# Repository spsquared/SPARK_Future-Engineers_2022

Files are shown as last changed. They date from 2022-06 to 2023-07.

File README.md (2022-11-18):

<div align=center>

banner

</div>

***

**Official GitHub repository for WRO USA team SPARK Future Engineers 2022. All code, documentation, and files are located here.**

Located below is the documentation, and a link to the build instructions.

***

# Contents
* [Hardware Overview](#the-hardware)
    * [Parts List](#parts-list)
    * [Assembly Instructions & Diagrams](#assembly)
    * [Photos](#photos)
* [Software Overview](#the-software)
    * [Operating System](#operating-system)
    * [Programming Language](#programming-language)
    * [IO](#io)
    * [Image Processing and Predictions](#image-predictions)
        * [Image Preprocessing](#image-preprocessing)
        * [Wall Steering](#wall-steering)
        * [Pillar Steering](#pillar-steering)
        * [Final Steering](#final-steering)
    * [SPARK Control Panel](#spark-control)
* [Team Photos](#team-photos)
* [Demonstration Video](#demonstration-video)
* [LiPo Battery Safety Notice](#lipo-battery-safety-notice)

***

# **The Hardware**

## Parts List
* [Schumacher Atom 2 S2 1/12 GT12 Competition Pan Car Kit](https://www.amainhobbies.com/schumacher-atom-2-s2-1-12-gt12-competition-pan-car-kit-schk179/p1055346)
* [HobbyWing QUICRUN 10BL60 Brushless ESC Sensored](https://www.hobbywingdirect.com/products/quicrun-10-sensored)
* [Fantom ICON V2 Torque Edition - Sensored Brushless Motor 25.5T](https://fantomracing.com/shop/motors/spec-motors/25-5-icon-torque-works-edition/)
* [12 Tooth 48 Pitch Pinion Gear w/Set Screw (3.17mm Bore)](https://www.amazon.com/Traxxas-PINION-PITCH-SCREW-2428/dp/B00EFXMUO2)
* [78 Tooth Spur Gear 48 Pitch](https://www.amazon.com/Kimbrough-Pitch-Spur-Gear-78T/dp/B0006O1QVM)
* [Xceed RC "Enneti" 1/12 Carbon Front Tires (2) (Carbon Black) (40 Shore)](https://www.amainhobbies.com/xceed-rc-enneti-1-12-carbon-front-tires-2-carbon-black-40-shore-xcd101708/p385419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)
* [Xceed RC "Enneti" 1/12 Carbon Rear Tires (2) (Carbon Black) (30 Shore)](https://www.amainhobbies.com/xceed-rc-enneti-1-12-carbon-rear-tires-2-carbon-black-30-shore-xcd101710/p385420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) OR [LEGO 49.5x20mm Tire (Part 15413)](https://www.bricklink.com/v2/catalog/catalogitem.page?P=15413) paired with 3d printed rims
* [Savox SV1260MG - Mini Digital High Voltage Servo 7.4V](https://www.savoxusa.com/products/savsv1260mg-mini-digital-high-voltage)
* [Woltechz LiPo Battery Balance Charger Discharger 1S -6S AC/DC for NiMH/NiCD/Li-PO/Li-Fe/Li-ion/PB](https://www.amazon.com/Woltechz-Battery-Charger-Discharger-Multi-Charging/dp/B07KDSGJFD/)
* [2x Zeee Premium Series 3S LiPo Battery 4200mAh 11.4V High Voltage Battery 120C with XT60 Plug](https://www.ebay.com/itm/384548969557)
* [2x Variable DC Voltage Buck Converter](https://www.amazon.com/Regulator-Adjustable-Converter-Electronic-Stabilizer/dp/B07PDGG84B/ref=sr_1_18)
* [Male 5.5mm DC Barrel Connector Pigtails](https://www.amazon.com/Pigtails-Female-Connector-Pigtail-Security/dp/B08PYWN3T7/)
* [DC Digital Voltometer](https://www.amazon.com/bayite-Digital-Voltmeter-Display-Motorcycle/dp/B00YALUXH0/)
* [Normally Closed Push Button Momentary On Switch (size must match)](https://www.amazon.com/Pieces-normally-closed-Button-Momentary/dp/B07HCLVMGS/)
* [Yahboom Jetson Nano 4GB Developer Kit](https://category.yahboom.net/collections/jetson/products/jetson-nano-sub)
* [Arducam Raspberry Pi Official Camera Module V2, with 8 Megapixel IMX219 Wide Angle 175 Degree Replacement](https://www.amazon.com/Arducam-Raspberry-Official-Megapixel-Replacement/dp/B083PW4BLH/)
* [Intel AX201 WiFi 6 BT 5.1 M.2 2230 with 10in RP-SMA Antenna (not required)](https://www.newegg.com/p/0XM-009Y-001C7)
* [Noctua NF-A4x10 5V (not required)](https://noctua.at/en/products/fan/nf-a4x10-5v)
* 20-24 gauge wire
* 25mm M3 brass spacers
* 20mm, 15mm M3 brass standoffs
* 6mm M3 nylon standoffs
* M3 nylon nuts
* 6mm countersunk M3 screws
* 6mm M3 nylon screws
* 4mm M2.5 screws

*Our build uses a different 25.5T brushless motor from HobbyWing but we had to modify our chassis to make it fit. The code will still work with the motor in this list.*

3D printed parts were used in our build, and all CAD files are located in the folder [/Documentation/CAD/](https://github.com/definitely-nobody-is-here/SPARK_Future-Engineers_2022/tree/master/Documentation/CAD). They're also linked here:
* [Platform](https://github.com/definitely-nobody-is-here/SPARK_Future-Engineers_2022/raw/master/Documentation/CAD/SPARK2022_platform.stl)
* [Camera Mount](https://github.com/definitely-nobody-is-here/SPARK_Future-Engineers_2022/raw/master/Documentation/CAD/SPARK2022_cameramount.stl)
* [Rear Wheel Rim](https://github.com/definitely-nobody-is-here/SPARK_Future-Engineers_2022/raw/master/Documentation/CAD/SPARK2022_rearwheelrim.stl) (if not using Xceed rear tires)
<!-- * [Camera LED Clip](https://github.com/definitely-nobody-is-here/SPARK_Future-Engineers_2022/raw/master/Documentation/CAD/SPARK2022_cameraLEDmount.stl) -->

The total estimated cost for the build is an eye watering $1050.00 excluding tools, 3D printers, computers, screws, wires, and standoffs.

## Assembly

We followed the instructions for the Atom 2 pan car kit, and then added the platform, wheels, and electronics. The ESC is VHB taped to the metal chassis, and the motor is mounted with the 12 tooth pinion gear. We swapped the stock 64 tooth spur gear to a new 78 tooth spur gear to lower our speed and give slightly more torque. The wires going to the voltage regulators can be soldered directly into the XT-60 connector with the ESC power leads. The voltage regulators and voltage meter can be screwed into standoffs with nylon screws on the upper platform.

The two RP-SMA connectors for the WiFi card (not required but good for development) can be routed to the back of the platform into their brackets. The NF A4x10 can be screwed into the heatsink of the Jetson NANO Developer Kit using 4 long nylon screws, but the holes will first have to be tapped or "tapped" by metal screws. The fan is also not required but can help (the board does reach fairly high temperatures at times).

The top platform is mounted onto existing locations on the car. In the rear two spacers are screwed into the mounting locations for the rear body posts. In the front, the screws for the bracket above the steering servo are replaced with standoffs.

The camera and LEDs are mounted on top of standoffs extending the top of front wheel plate.

#### **For a detailed build guide, go to [ASSEMBLY.md](./ASSEMBLY.md)**

Here is a simple electromechanical schematic for how the electronics are wired:

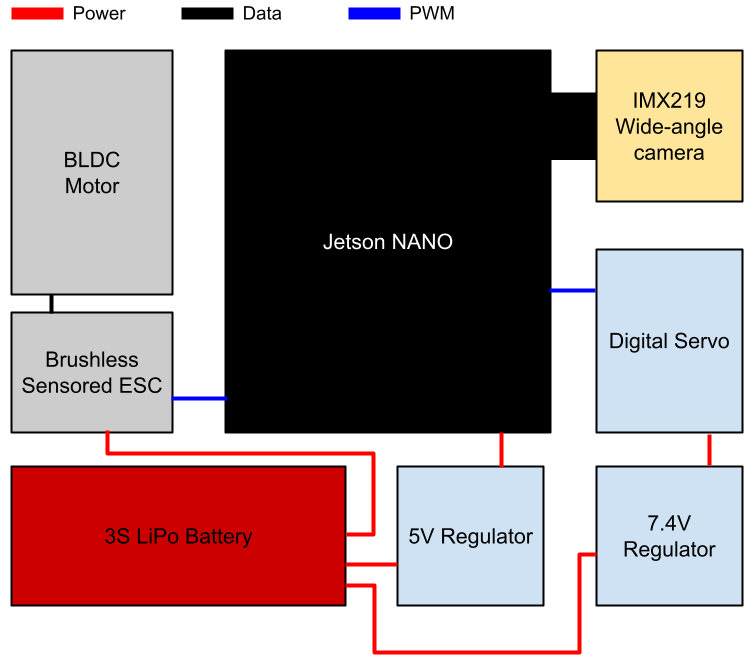
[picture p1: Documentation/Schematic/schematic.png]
Schematic


***

## Photos
| | |
| --- | --- |
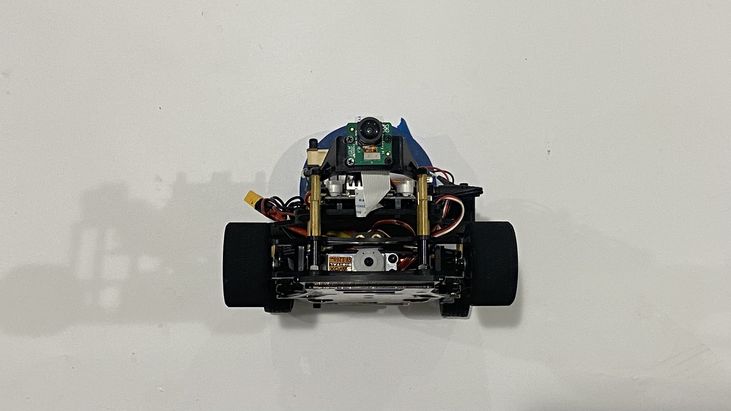
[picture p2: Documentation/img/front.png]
front
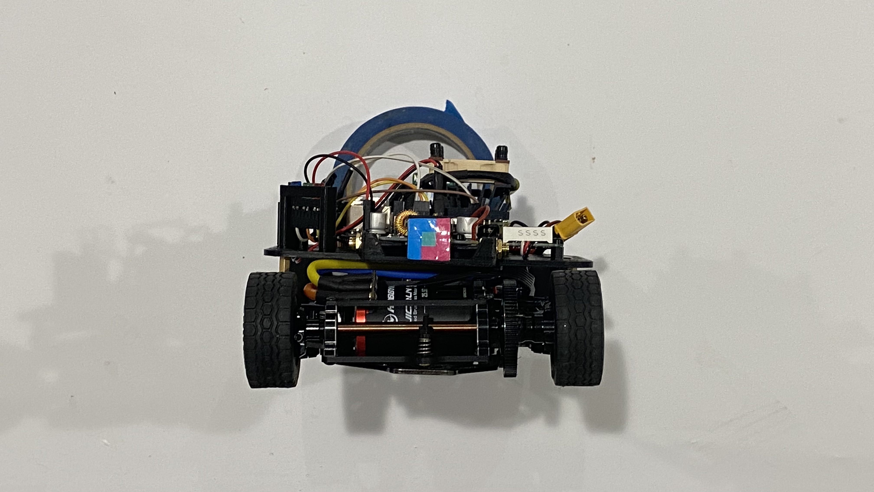
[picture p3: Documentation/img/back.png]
back
|  |  |
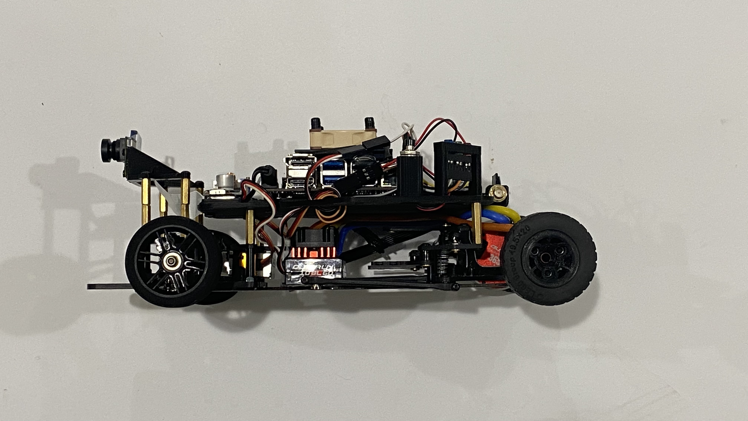
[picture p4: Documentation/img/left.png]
left
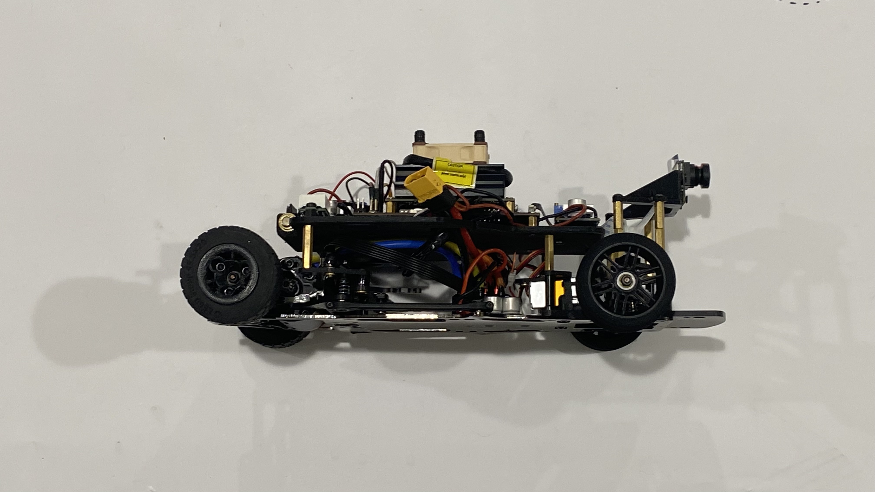
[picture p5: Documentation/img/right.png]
right
|  |  |
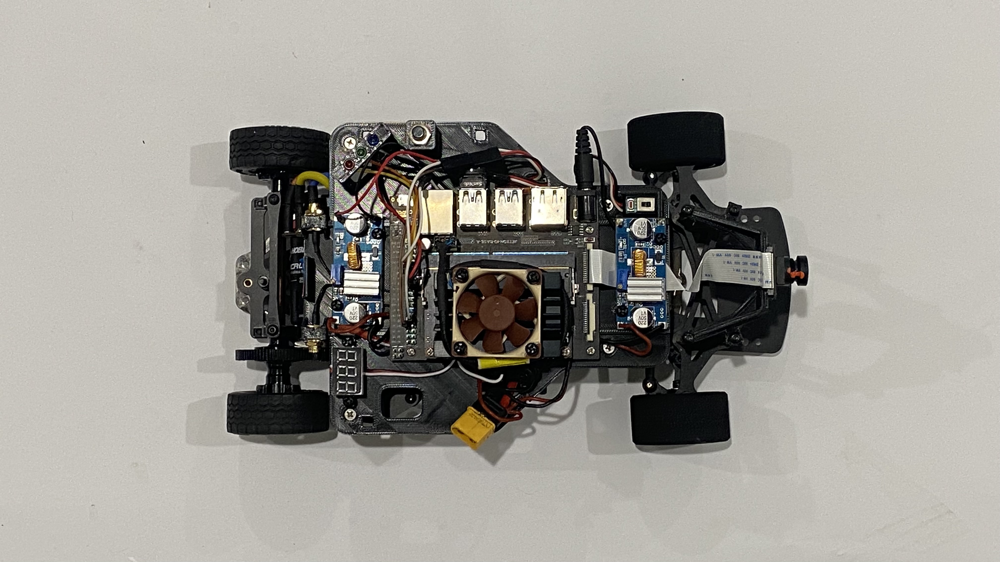
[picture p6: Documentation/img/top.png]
top
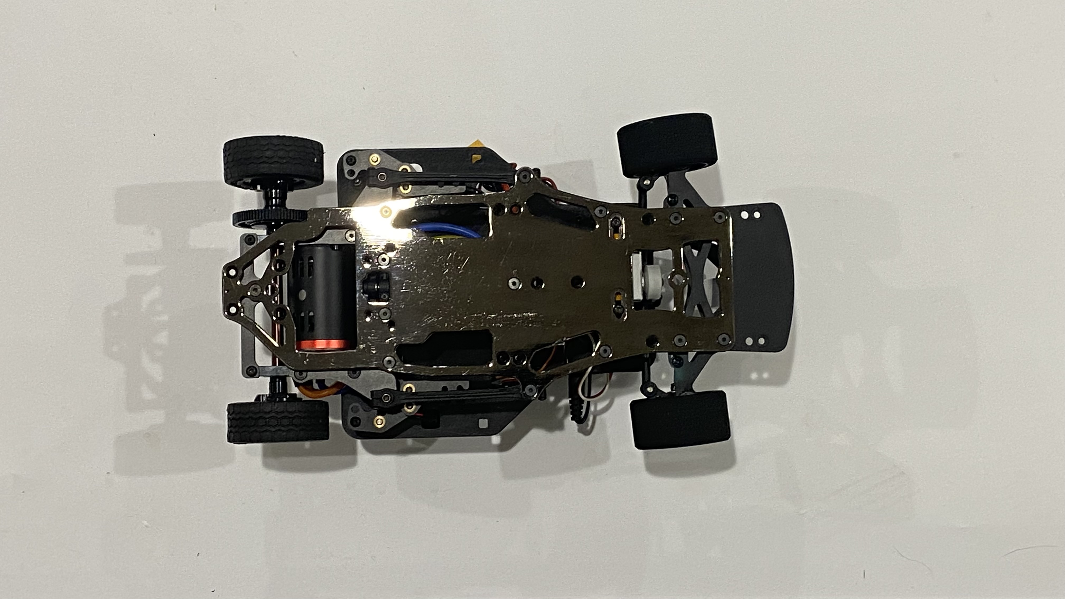
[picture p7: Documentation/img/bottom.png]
bottom
|  |  |

***

# **The Software**

## **Operating System**

We used Jetson Nano's operating system, which is Ubuntu 18.04. It has been changed to text-only mode to remove the unneccesary GUI. We also added a startup script ([see "Board Setup" in Assembly.md](./ASSEMBLY.md#board-setup-sshfs-and-static-ip)) to run the program on startup, which waits for a button press before running the program.

## **Programming Language**

All our code is in python (except the SPARK Control Panel and SPARK Randomizer, those are HTML/JS/CSS documents that aren't uploaded or used in runs). We use `os`, `time`, `threading`, `numpy`, `cv2`, `base64`, `threading`, `asyncio`, `Jetson.GPIO`, `jetcam`, `json`, `websockets`.

The **entire** `Program` directory must be uploaded in order for the program to run.

## **IO**
The camera is handled by the `jetcam` library, which we can read the most recent frame into a `numpy` array, which we then process.

The drivetrain of the car is handled separately by the controller in the servo and the ESC. We feed them a pulse of a specific width (time) to control their speed/angle. However, due to a software limitation in the `Jetson.GPIO` library, we only jave 5 throttle steps, meaning we don't have as fine throttle control as desired. This can possibly be fixed with a solution that could be described as "hacky", however we haven't tried it.

***

## **Image Predictions**

All the code for image filtering and predictions can be found in `/Program/AI/filter.py`.

### **Image Preprocessing**

The filter function takes in a raw image and outputs a filtered image. This image is filtered based on 6 HSV values, `redMax`, `redMin`, `greenMin`, `greenMax`, `blueMin`, `blueMax`. Using `cv2.cvtColor`, we can convert the RGB image captured by the camera to a HSV image. HSV stands for hue, saturation, value. Using `cv2.inRange`, we can filter the image based on these values, to get a mask of the pillars. The blue mask is used to detect the blue lines on the ground. There used to be another pass to filter in the walls, but that was phased out in favor of a new method. This method is unreliable in spaces with dark areas and places with a lot of glare. Instead, after using `cv2.cvtColor` to turn the image into a grayscale image, `cv2.GaussianBlur` to blur the image, we use `cv2.Canny` to get a black and white image highlighting edges.

### **Image Predictions**

The predict function is where all the predictions happen. There are three sections to it, pillar steering, wall steering, and turn detection.

#### **Pillar Steering**

Pillar steering starts by creating a blob detector using `cv2.SimpleBlobDetector` and using `SimpleBlobDetector_Params` to set the parameters. Using the filtered red and green images, the blob detector detects blobs to filter out random noise in the image and get the relative position and relative size of the pillars. We have two equations, `getRedEquation` and `getGreenEquation`. These calculate if we will hit a pillar or not, and we use it on all the blobs detected by the blob detector. If there are pillars detected, we take the largest pillar. Using a combination of the size of the pillar and the location of the pillar, we calculate a steering value on which direction we should turn. This is stored in `pillarSteering`. The steering value is also written in `passedPillar`, as `passedPillar` is used when we pass a pillar to prevent the back wheels from hitting the pillar.

#### **Wall Steering**

Next we have wall steering. First we start by cropping out the top 79 pixels. Due to the way the camera is placed, it is exactly the same height as the wall, so no matter where the wall is, the top line is nearly constant, and is around 79 pixels. After this, we swap the axes to prepare for wall height detection. Using `numpy.argmax` we find the bottom of the wall. We split the image into 8 sections. Taking the differences, we can find the slope of each section, and catagorize the sections. If the slope is less than -0.2, it is catagorized as a left wall. If the slope is more than 0.2, it is catagorized as a right wall. Otherwise, it is catagorized as a center wall. The first two sections on the left side are always left walls and the first two sections on the right side are always right walls. If there is a sudden jump in the height of the wall, we know the higher wall cannot be a center wall, and must either be a left wall or a right wall.

Now, we loop through all 8 wall sections. Based on the position and height of the wall, we calculate a steering value. At the end, we have 3 values, one for all the left walls, one for all the right walls, and one for all the center walls. We take the maximum.

#### **Final Steering & Lap Direction**

On the first frame, we look for a jump in either the left wall or the right wall. This tells us if we are driving clockwise or counterclockwise, as the side with the jump must have a gap in the wall.

A negative steering value means we turn left, while a positive means turning right.

Finally, we have turn detection. If there are more than 500 blue pixels on the screen we increase `turnsMade` by one, and if we have turned 12 times, or 3 laps, it returns "stop", causing the car to stop.

After this, we send all this information to SPARK Control.

Finally, it takes the sum of the pillar steering and wall steering and returns it.

***

## **SPARK Control**
SPARK Control is our own testing and debugging software. It consists of a WebSocket server running on the Jetson NANO, and a local HTML document on our computers. The page uses a WebSocket connection to communicate with the server. The server can broadcast and recieve data in the form of JSON strings, which allows for the differentiation of events and more complex data transfers. The system is modular and is simple to use. As long as the data can be converted to JSON, it can be sent. Broadcasting is as simple as specifying an event name and some data to be sent. To recieve messages, it is possible to add an event listener, which is a function that is run when the specified event is recieved.

The client control panel consists of a log, which is appended to by the `message` event; filter tuning sliders for changing the ranges of the image preprocessor; capture buttons to save and stream raw and filtered images, and the ability to control the vehicle when running in manual drive mode. The data display can show raw and filtered image streams from the car's camera, visualize the detected blobs and wall heights, and display output data from the code. By default, the last 500 frames of data are saved in history and can be replayed for debugging.

<div align=center>

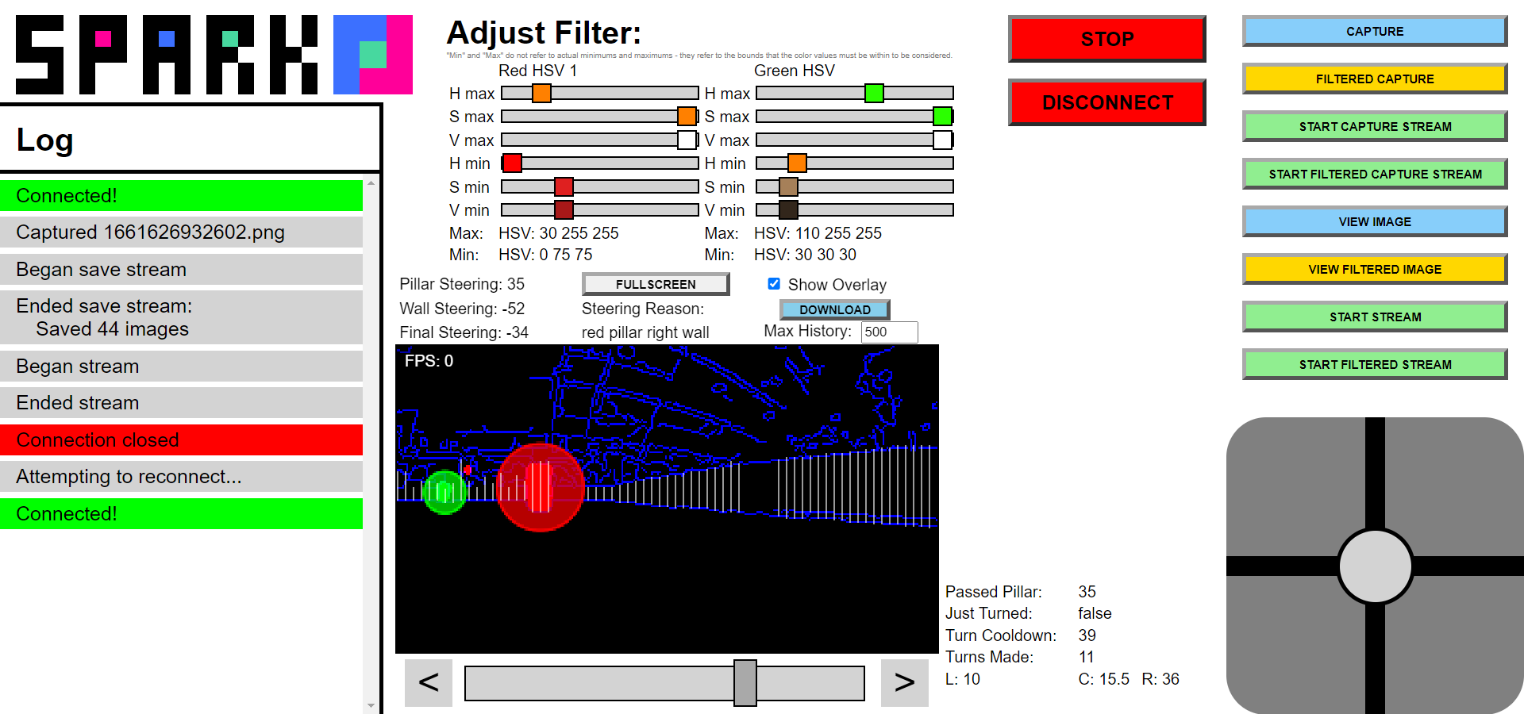
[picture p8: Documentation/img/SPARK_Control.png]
SPARK Control Panel


</div>

To connect to the robot, obtain the IP address (set to static in the assembly instructions) of the robot, and open `/SPARK-Control/index.js`, and change line 1's value to the ip.

Example:

```
const ip = '192.168.1.151';
```

It's possible to use SPARK Control to change the filter colors to adjust to the environment. Simply change the HSV sliders and use the "View Filtered Image" button to see the effects of your changes. Afterwards locate the color assignments in `/Program/AI/filter.py` and change them to match your environment.

Example:

```
rm = redMin = (0, 95, 75)
rM = redMax = (25, 255, 255)
gm = greenMin = (30, 30, 40)
gM = greenMax = (110, 255, 255)
bm = blueMin = (90, 80, 70)
bM = blueMax = (140, 255, 255)
```

You can update the defaults in `/SPARK-Control/index.js` as well in `initcolors`

Example:

```
let initcolors = [
    [
        25, 255, 255,
        0, 95, 75
    ],
    [
        110, 255, 255,
        30, 30, 40
    ],
    [
        140, 255, 255,
        90, 80, 70
    ],
];
```

**Don't forget to upload the `Program` folder again!**

***

# Team Photos

The one to the left is Jie Gao in 10th grade.

The one to the right is Maitian Sha in 9th grade.

We are both in West Windsor Plainsboro High School South.

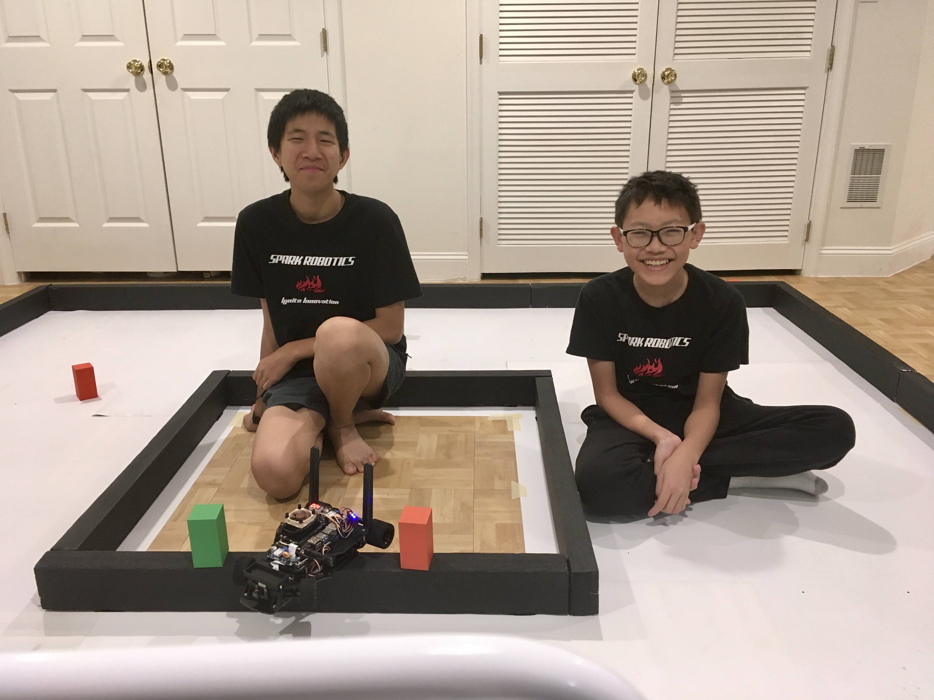
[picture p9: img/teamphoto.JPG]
normal photo

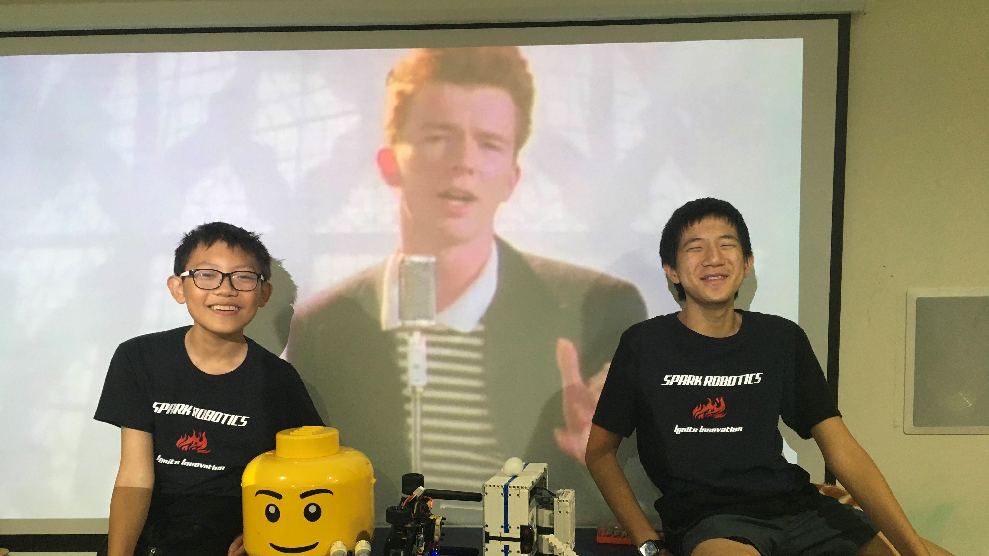
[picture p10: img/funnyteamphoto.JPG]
rick astley


***

# **Demonstration Video**

[Demo video: Display video](https://youtu.be/4ExFMHKP9r8)

[Demo video: No traffic signals, normal walls](https://youtu.be/QAQedR-BHWs)

[Demo video: No traffic signals, normal walls, video #2](https://youtu.be/lzBcYp8RJO0)

[Demo video: No traffic signals, extended walls](https://youtu.be/rsylY0rOz3Y)

[Demo video: With traffic signals](https://youtu.be/jMQYSYyJUZc)

[Demo video: With traffic signals, video #2](https://youtu.be/7_S408GaNl4)

# LiPo Battery Safety Notice

While LiPo batteries are the safest form of portable, affordable, high density energy storage, there are still precautions to be taken when working with them. Lithium is a highly volatile element, and will react with the water vapor in the air if exposed to it.

1. **Do not** puncture, deform, short, or heat LiPo batteries above 80° F
2. Store and charge LiPos in a *fireproof container* **away** from flammable materials and water
3. **NEVER** charge a swollen or damaged battery (e.g. damaged leads, swelling of cells, puncture in wrapping)
4. **NEVER** leave a charging battery unattended
5. Only charge LiPo batteries with chargers *designed for LiPo batteries*
6. Dropping a battery can cause sufficient damage to rupture a cell and cause shorts
7. Overdischarging a LiPo battery can cause **permanent damage**

If a LiPo battery goes below its minimum voltage (stated in the manual included or 3.3v multiplied by the amount of cells connected in series) it can cause **permanent internal damage**. This damage is not visible until after further use, when it can swell, or potentially burst and **cause a FIRE**.

**Read all safety notes and instructions included with LiPo batteries before use.**

### For a more detailed LiPo safety manual there is one on [Tenergy Power](https://power.tenergy.com/lipo-safety-warnings/)

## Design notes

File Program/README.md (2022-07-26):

# SPARK WRO 2022 Future Engineers Program Documentation

This is the documentation for all the source code used for the USEL Future Engineers 2022 season.

The code is divided into multiple modular files. `IO` contains source code for camera input and PWM control for throttle and steering. `Util` contains source code for development utilities and is mostly not needed for autonomous driving. `AI` contains source code for computer vision.

During matches, the `server.py` file in `Util` will not be uploaded to ensure compliance with rule 10.9

### How we Implemented Computer Vision
We first start with an edge detection algorithm on the walls. At the same time, we filter the images to find the walls (black pixels) and traffic signs (red and green pixels). The resulting image is a black rectangle with RGB values representing where the objects are

<!-- maitian insert the images here -->

The resulting filtered image is then sent to the TensorRT model to determine the steering output.

In training, if the outputted steering values doesn't match the recorded steering values for an image, the model is penalized and given the correct steering values. This is an example of reinforcement learning being combined with unsupervised learning - the model is trained on images and recorded data and then tested on new images and data.

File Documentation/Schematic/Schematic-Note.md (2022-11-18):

Read [ASSEMBLY.md](/../ASSEMBLY.md) for more detailed information.

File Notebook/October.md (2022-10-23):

# October 2022
SPARK WRO 2022 Future Engineers Engineering Notebooks

***

# 10/1/22
We did work on wiring the LEDs. The plan is to use the BEC output of the ESC to supply 6V to the LEDs, which can draw up to 2 Amps, so in theory the BEC should be able to drive them. When the ESC is switched off, the BEC output is also off, so we won't waste battery when idling. Also, we're printing the new platform, which prints way slower than it could be printed because the layer height is uselessly thin and the top-bottom speed is too low.

# 10/2/22
Terrible print quality. 20 hours. Nothing fits except for the screws. Actually, not even the screws fit. With the same dimensions, somehow the screw holes don't line up, the antenna mounts are the wrong size, and the switch inset is 1mm too small even thought it was sized 1mm up.

Also, the LEDs are so bright that they overheat and draw too much current.

# 10/5/22
Today we worked on improving the new system. It can now discern whether a wall is in front of the car or to the side. Mostly. There are cases where it turns to almost face the inner wall and attempts to turn the wrong direction, thinking that it's reached a turn.

# 10/6/22
New wheel design - we're switching to LEGO wheels - or more specifically, their 49.5x20mm tires. We modified our existing rim to fit the new tire, which is slightly larger. We did this because the spur diff gear touches the ground when we drive on our existing wheels, which can cause damage to the gear and also collect lots of dust.

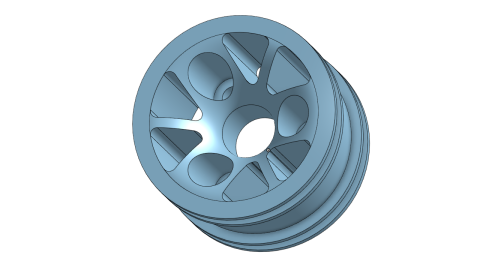
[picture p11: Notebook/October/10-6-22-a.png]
wheel v3


# 10/9/22
The lights are so bright that they're causing some issues. The reflection off the mat is strong enough to cause the brightness to lower and the colors to change. We can combat this by placing a shield on the bottom preventing light from reaching the floor.

# 10/17/22
We don't need lights anymore. We've decided that lights will be unneccesar, and the competition mat should be evenly lit. We'll remove the lights and change nothing else.

# 10/22/22
Got new motor. Does anyone even read these?

It's a lot slower (less than half the speed) but doesn't fit in the chassis. We may have used a dremel to make it fit.

Details: We got a quicrun 3650 because it has a lower kV rating and will allow us to move at lower speeds. However, the motor is barely short enough to fit in the mount, and if the car is rolled left, the motor gets stuck and the car is left with a permanent left roll. We considered preventing roll on the rear axle completely by locking it with bolts but the threaded inserts on ours are broken and we can't remove the springs to replace them with bolts. Our solution was to grind off 1mm of material on the cutout in the frame.

It still doesn't fit because the protrusion is 15mm, while the maximum allowable protrusion is 10mm. So now we either keep using the old one (and unsolder connectors) or buy a new one (and unsolder connectors). And now we have a patch of exposed steel in the chassis.

Instead of choosing either of those options, we ground away more of the chassis instead.

To avoid putting "grind off part of the chassis" in the instructions the 22.5T version of the original Fantom motor will be used instead.

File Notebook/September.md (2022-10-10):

# September 2022
SPARK WRO 2022 Future Engineers Engineering Notebooks

***

# 9/17/22
We've recieved the email that we're competing in the internationals this year. We have some proposed changes to be made:
- Redesign camera mount to be higher up, making it easier to judge the location of walls
- Add LEDs to reduce the effects of uneven ambient lighting
- Change wall detection code to check the slope of the detected walls instead of assuming the locations based on the area of the image it's in
- Reduce thickness of rear wheels to prevent them from knocking over traffic signals we drive past

A new camera mount was designed; it used the four posts that the upper steering knuckle support uses rather than the holes for the body posts. There are indents in the forward screw holes on the bracket to allow for the new LED mounts.

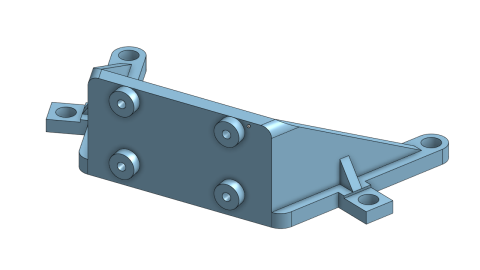
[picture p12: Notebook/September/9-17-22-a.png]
new camera mount


# 9/18/22
Printing the new camera mount proved to be more difficult than expected. There was dust on the filament because we had left it sitting in a corner, making the extrusions messy and making half the print unusable. The printing speed may have been too fast, and the cooling fan couldn't cool the extruded material fast enough, resulting in warping and more messy spots. The messy edges of the print meant that the LED clips that fit over the mounting hardware doesn't fit.
On the positive side, the mounting holes lined up really well and the camera seems to be in a much better position with this bracket.

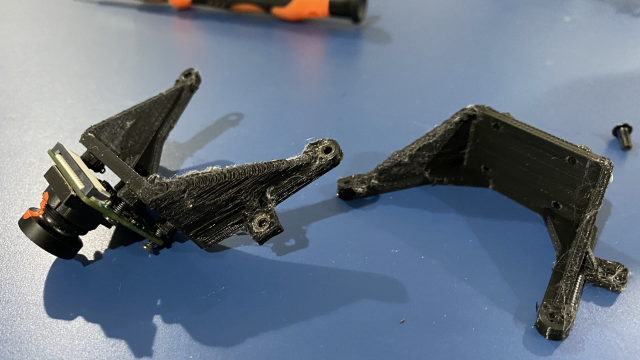
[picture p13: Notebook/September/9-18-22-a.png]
messy prints


Also, there aren't any 1:12 scale 40mm wheels for our specific mounting pattern, so we ordered some tires off of Amazon and began designing our own wheels.

# 9/19/22
Below is the final design for our custom wheel hub. It has a small diameter of 28mm to fit the [new wheels](https://www.amazon.com/gp/product/B09YHC4NDS/).

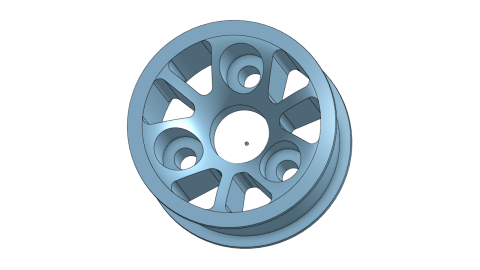
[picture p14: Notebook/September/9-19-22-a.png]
new wheel hub


The first print was "alright". The wheel fit onto the hub and the screw holes lined up. The hub is a bit too wide and is missing extra insets for the M3 bolt heads used to hold it onto the axle.

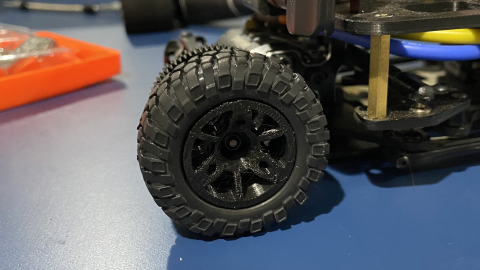
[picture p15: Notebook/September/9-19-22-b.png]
test fit of prototype hub


# 9/20/22
Multiple different prints resulted in unusable results. The inside face of the wheel hub was recessed to reduce the profile of the wheel (by 1mm) and without supports, it would collapse immediately. With supports, they're unremovable and the slicer places excessive amounts of them. There's still warping as well.

# 9/24/22
Yesterday the wheels finished printing. Today we put them on. Now we have wheels. The prints were warping slightly, but they were still usable. The camera bracket, on the other hand, warped so badly that none of them were actually good. The issue is that since the object is so small with so many details, the print head spends more time there, putting more heat into the already extruded material, melting it. This happens every time a layer is added, resulting in warped and messy prints. The solution was to lower the extrusion temperature to 180 degrees Celsius so it wouldn't add too much heat to existing material but also still melted the PLA being extruded.

We also got a set of [5W LEDS](https://www.amazon.com/6000K-6500K-600mA-700mA-Intensity-Components-Lighting/dp/B01DBZJBIW), which we will design a mount for today. The idea is to put a recess in a plate with holes for the tabs on the sides to pass through. The tolerances for this method are really tight, though.

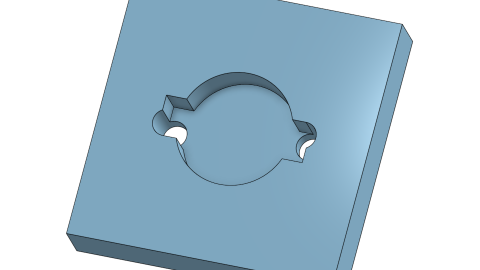
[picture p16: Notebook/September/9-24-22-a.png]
LED bracket test


We also made a fifth revision of the top platform, integrating the indicator LEDs and the new start button into the plate (as well as some space for our logo).

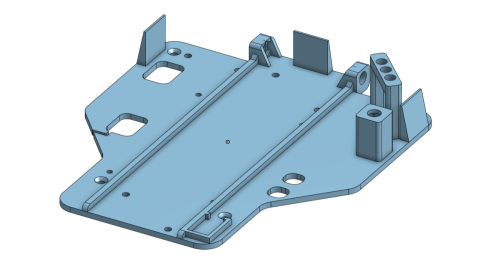
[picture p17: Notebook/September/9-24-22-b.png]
platform v5


# 9/26/22
Today a battery was found to be at 0 volts. Not sure if it's still safe to use, people on the internet say that it could catch fire if charged. Hopefully that doesn't happen.

In other news, we're working on improving the wall detection code. Instead of assuming that the right side of the image is always going to be a right wall, the left always the left wall, and the center always the far wall in front, we now divide the image into 6 sections, and check the slope of the wall in each section using the [RANSAC Regression algorithm](https://scikit-learn.org/stable/modules/generated/sklearn.linear_model.RANSACRegressor.html). This will reduce the chances of a false detection. For example, in a turn of one specific case a wall in front of the car was assumed to be to the right of the car, so it turned left because "the right wall is huge".

In even more other news, the new camera bracket and LED brackets are mounted on 35mm brass standoffs extending up from the top of the front wheel plate.

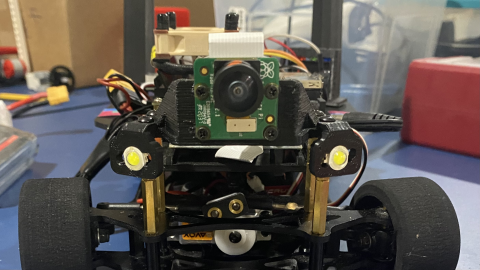
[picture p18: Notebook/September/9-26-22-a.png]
mounting of camera bracket


The LED brackets are sandwiched between the screw and the camera bracket, and is locked in place by the negative imprint of the camera bracket "foot".

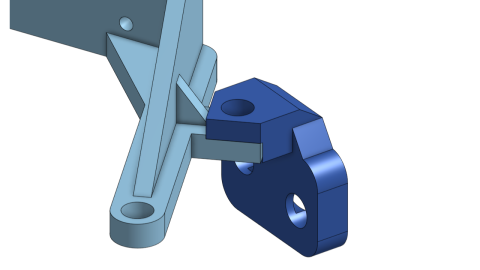
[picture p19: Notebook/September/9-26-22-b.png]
mounting of LED bracket


I'm bad a crimping. And spelling. "Componenents".

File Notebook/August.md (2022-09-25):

# August 2022
SPARK WRO 2022 Future Engineers Engineering Notebooks

***

# 8/1/22
At this point we are trying to make the car drive around traffic signals. We added the detection for traffic signals and turning accordingly. We encountered some conflicts, where the car would have to turn left but refuse to since it wants to stay in the center of the path. Sometimes the traffic signals would appear too small in the filtered image and then blob detection ignore it, assuming that it's a filtering error. There were other issues, like typos. Those were relatively simple fixes, and now we can reliably sort of drive around the course.

# 8/4/22
Today we fixed some bugs and added a live video stream from the car. The blob detector had an issue where if the blob is touching the edge of the image, it wouldn't detect it. We solved this using cv2 to create a border around the image. We added a live video stream from the car to make debugging easier, since it can display the live feed from the camera, the filtered image that the car processes, and the blobs detected, all on the screen. In the future we plan to display more data on the screen.

In other news, we orded a wide-angle camera, and it arrived today. A new mount was 3D-printed to accomodate the larger lens (huge in comparison to the narrow-frame IMX219).

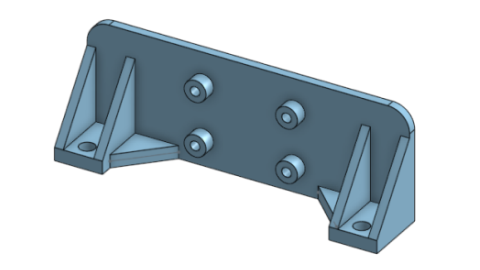
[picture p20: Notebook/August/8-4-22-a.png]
new camera mount


# 8/5/22
We attempted to switch to the wide-angle camera, but the edges of the image are tinted pink. So, we can't use it.

camera outside world border lol

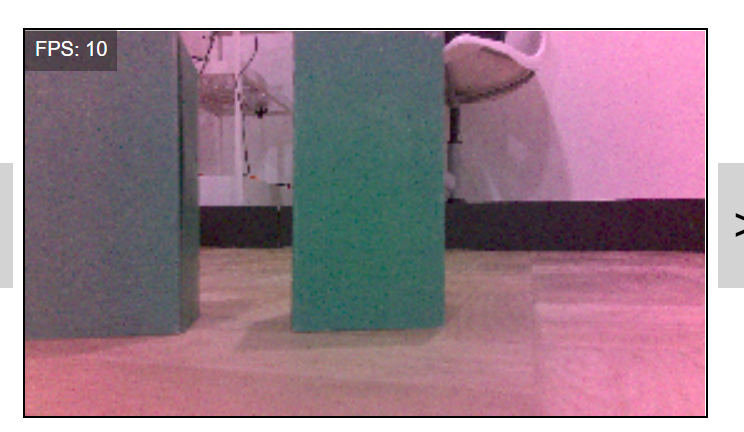
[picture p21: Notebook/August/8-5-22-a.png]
pink fringing on camera


In other news...
The car now drives exceptionally well.

We changed the steering values from an absolute return value to a weighted value; the steering values are scaled by size (which is correlated to distance) from the car. When the car is further away from something, it has less incentive to turn. Turn values are calculated individually for the red signals, green signals, left wall, and right wall. The program determines the final steering value by choosing the steering value that has the largest absolute value. This reduces the chances that the car overcorrects and ends up turning so far it can't recover before hitting a wall, and also prevents premature and most unneccesary turns.

# 8/8/22
Our camera broke and we got new signals. Again. The new red signals are unusually orange, leading to the filter detecting people's skin as red. We tuned the filter again and discovered some new problems. The program doesn't do any localization, so once it stops detecting something, it completely forgets it exists. We can add a simple memory system that "remembers" that it saw a signal, and will continue to act as if it is on screen for some time after it stops detecting it, preventing it from turning and running over a traffic signal as soon as it's out of view.

# 8/12/22
Today we installed a wide-angle camera. To us, distortion is not an issue, since the size of objects will be the same as long as the distance is the same, and that's all we need. We just have to recalculate the inequalities used for predicting collisions.

# 8/13/22
Tuning the prediction - We added a check for whether a wall was the inner wall or outer wall. When the car drives straight towards a wall, it cannot use the slope of the wall to decide whether it is the inner or outer walls.

# 8/14/22
More tuning, but we also made some other changes. We resolved an issue that we have had for a long time, and will probably exist at competitions. When there is a black (or sufficiently dark) area in the image, it gets filtered out as wall and skews wall height readings, making it hard for the car to determine when to turn. We decided that instead of using the wall height - nonzero values in a vertical strip of the image - we would look at the locaction of the bottom edge of the walls, which is simple since there are no stray pixels or false positives on the floor. Also, we didn't implement any memory systems. There were numerous bugs in the process, like seemingly random turns and steering values of 14000.

There would be a video of the car here, but we haven't had the chance to take any good videos yet.

I don't think we have any screenshots of our debugging and development software, called SPARK Control, here. Here's a screenshot now:

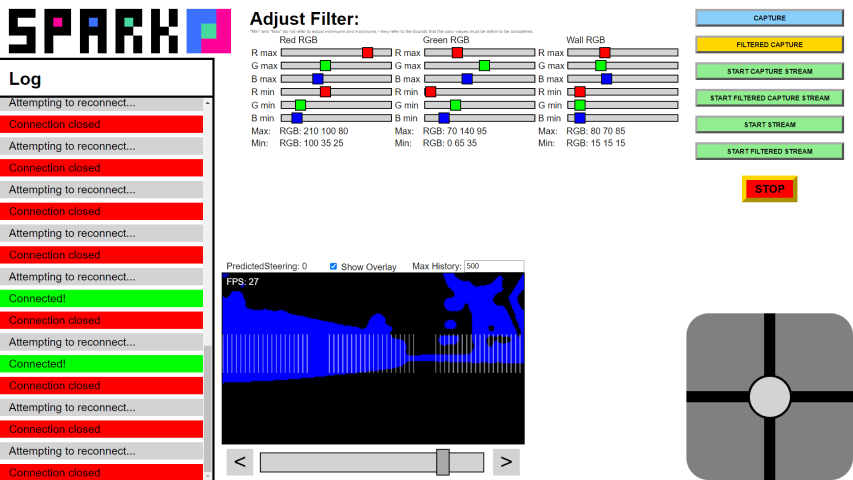
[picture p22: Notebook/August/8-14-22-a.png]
SPARK Control Panel


There is a more detailed description in the documentation.

# 8/15/22, 8/16/22, 8/18/22, 8/19/22, 8/20/22
More tuning. Not a lot of new things.

# 8/21/22
We switched our systems to a new network (pocket router) and now the camera isn't detected.

# 8/27/22
Haven't been updating logs in a while, but we're at the competition now. We had issues with lighting, including glare and hard shadows. We've switched to using HSV as our pillar detection, and implemented a better system for detecting walls. In short, we find edges by marking pixels with high contrast, and then finding the first sets of highlighted pixels from the bottom. This method is much more reliable than using the color and works well in most lighting conditions.

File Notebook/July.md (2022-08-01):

# July 2022
SPARK WRO 2022 Future Engineers Engineering Notebooks

***

# 7/2/22
We attempted to get the Jetson to boot off of a USB drive, as the built-in EMMC doesn't have enough capacity to install the Jetpack SDK. The large 78-tooth diff gear was installed as well.

### Updates
* Successfully changed the boot manager to boot from USB
* 78-tooth diff gear installed

There were issues installing it, as before in mid-June we attempted to do this as well. There were initial issues using NVIDIA's SDK Management tool, as it couldn't find any compatible versions of JetPack for Ubuntu 20.

# 7/4/22
We set up Tensorflow and began working on making a test dataset and making GPIO PWM work.

### Updates
* Following guide to setting up and using TensorFlow.
* The 128GB card was flashed, so we now have a lot more storage available.
* Did some testing to try and get GPIO pins working and also making TensorFlow work.

We used the [guide](http://www.yahboom.net/study/jetson-NANO) supplied by Yahboom to set up our environment. We only needed steps 1.3 and the first 1.4, which for whatever reason step 1.4 came before step 1.3, and there was a second step 1.4 after step 1.3. Afterwards we went through section 3, with minimal issues. It completed the test program with flying colors, so we moved on to trying to create a training data set using the camera. We ended with the camera able to capture an image, though unencoded and therefore uncompressed.

Meanwhile, work was being done to test the GPIO. We plan to use the [jetson-gpio](https://github.com/NVIDIA/jetson-gpio) library to control the pins. It installed fine, but we were unable to actually control any of the pins. We eventually found that the BCM and BOARD pinouts were slightly different, and we were able to turn on and off LEDs with the GPIO. Whether the PWM pins work or not is to be found, but we will need to find the correct pinout for this carrier board or we will not even be able to find the pins.

Below are links to the video.

[Link to video (download)](./July/7-4-22-a.mp4)  
[Link to video (download 2)](https://raw.githubusercontent.com/definitely-nobody-is-here/SPARK_Future-Engineers_2022/master/Notebook/2022/July/7-4-22-a.mp4)

# 7/9/22
Some changes and additions.

### Updates
* Jetson NANO has issues booting
* Improvements to platform
* Addition of a WIFI/Bluetooth card

On 7/7/22 we discovered that the Jetson NANO wouldn't boot anymore. Once plugged in it would give the error `****NvRmMemInit failed****` and refused to boot. Today we plan on flashing a second NANO and using that instead, returning the original one.

In other news, a refresh for the platform is to be done, with changes to improve wire management and the addition of an LED display to monitor voltage and a WIFI/Bluetooth card and antennas. We will have to start shaving weight if we keep adding more things, however. We're approaching the limit at 1.4kg. The WIFI and Bluetooth antennas won't be used in competition since they serve no use, so they must be easily removable. We started by testing the coaxial connector attachement points, which were modeled specifically for our connectors.

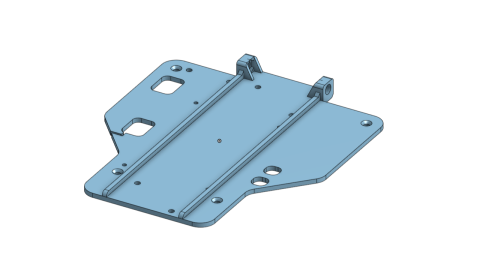
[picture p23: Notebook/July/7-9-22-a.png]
Platform V4


# 7/10/22
We encountered the meminit error again after changing out the NANO and platform.

### Updates
* Rebuilt top platform with new NANO and platform
* WiFi added
* PWM works

##### New platform

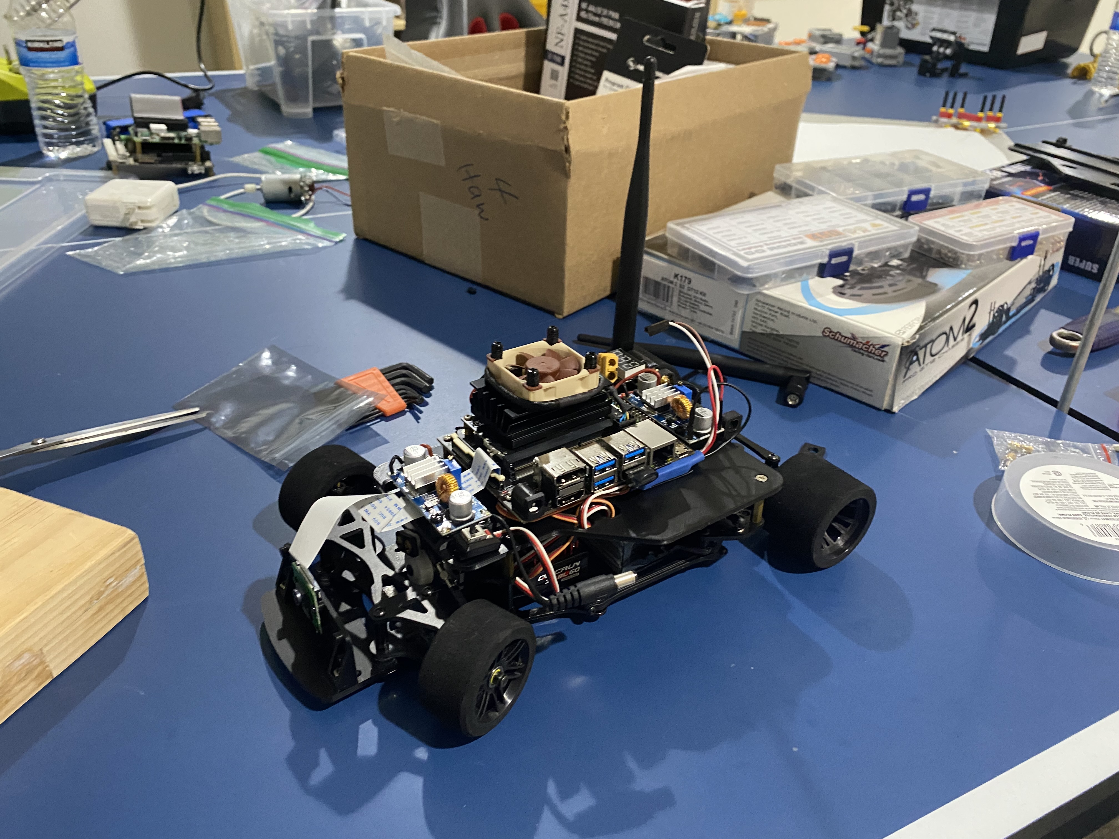
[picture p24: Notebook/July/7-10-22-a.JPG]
Rebuilt platform


##### PWM

We managed to use PWM. Initially the io config program (jetson-io.py) would crash every time, so we weren't able to enable PWM. After a lot of editing and changing files that should not be changed, we managed to enter the menu for GPIO configuration. The issue was caused by the board reporting a slightly different version than the library supported, being a revision of the board and therefore technically not supported. It reported as p3448-0000-b00+p3449-0002-b00 while the closest supported board was p3448-0000-b00+p3449-0000-b00. This is because our Developer Kit is the slightly updated version of that board. We were able to bypass the files by copying and renaming a .dtb file in `/boot/dtb` and then hardcoding some parameters in `/opt/nvidia/Utils/dtb.py`. And after that, we were able to enable PWM.

The PWM works, as shown in the video below of the PWM changing the effective voltage being read by the multimeter.

[Link to video (download)](./July/7-10-22-c.mp4)
[Link to video (download 2)](https://raw.githubusercontent.com/definitely-nobody-is-here/SPARK_Future-Engineers_2022/master/Notebook/2022/July/7-10-22-c.mp4)

As can be seen in the video linked below (twice) the PWM works to control both the servo and ESC, but with no accuraccy.

[Link to video (download)](./July/7-10-22-b.mp4)
[Link to video (download 2)](https://raw.githubusercontent.com/definitely-nobody-is-here/SPARK_Future-Engineers_2022/master/Notebook/2022/July/7-10-22-b.mp4)

A major issue is that if done wrong, the motor will actually draw so much current that the voltage drops low enough to make the NANO shut down. Of course we will electronically limit the current draw of the motor so this doesn't happen, and it's not like we will go that fast anyways.

A slightly less major issue is the issue of calibration. The servo and ESC have an acceptable range of pulse width, and so we must change the min and max duty cycles to be able to control them.

# 7/14/22
We got the PWM values!

The min and max PWM values have a suprisingly narrow range. The steering has a range of 15% (at 100Hz), and the throttle goes backwards in the range of 15%-30%, and 30
% to 45% is the forwards range. At 100% throttle the motor still draws enough current to make everything shut down, so we limited it to about 30%, which is still too fast anyways. There is one problem: The motor has very little torque at low RPM, even though it is supposed to be a sensored motor. We have the highest reduction ratio we can fit on the car, so we can only limit throttle at this point. There is also a slight rattle coming from the gears - perhaps something is a bit loose.

Below is a video of the steering

insert videos here

# 7/16/22
Trying to get some sort of control. We ended up disabling the ui to prevent the "NvRmMemInit" error, but now we discover a new issue. We have to log in to the Jetson NANO in order to use SSH, meaning we still have to use a screen and a mouse and keyboard to boot. In other news, we cut some foam board for the walls of the map.

# 7/17/22
We can now stream 5fps video to Jupyter Notebook! We got these images:

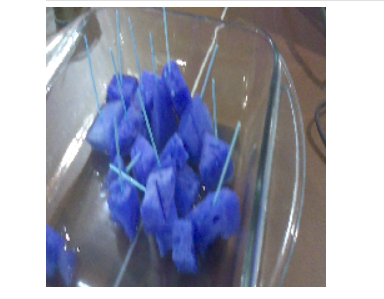
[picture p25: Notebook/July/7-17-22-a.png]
Blue watermelon

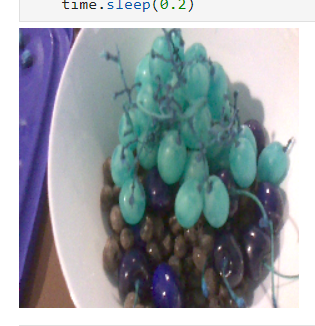
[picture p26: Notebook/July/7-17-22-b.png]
Cyan greps


The color format is BGR so so the red and blue color channels are swapped - not that it matters, since we don't really care about color.

# 7/21/22
Small update - working on integrating camera and control code into packages for actual use, as well as a WiFi card swap so we can stream the video live while testing. We encountered some driver issues along the way and used the answer posted on [this thread](https://forums.developer.nvidia.com/t/intel-9260-wifi-on-jetson-nano-jetbot/73360/74) by "idcrook" on 7/24/2019.

Jupyter lab also isn't working somehow.

# 7/23/22
Today we gathered training photos for the AI. To do this, we drove the car around the course manually using a control app we designed while continuously saving pictures to a folder.

The control app is a local HTML page that uses a WebSocket to connect to the car, which we added a WebSocket server to. The app currently can be used to control the car with WASD or a (very difficult to use) joystick, and there is a log on the left side, which is currently non-functional. There are plans to use the app to allow us to view and debug what the AI is doing as the program is running using a live stream.

Progress in code includes a better server and control page. This makes development easier since it allows us to collect training data much faster when everything is integrated into one app.

Issues we ran into:
* The camera could not initialize, since it was "busy". The Jupyter kernel was continuing to use teh camera even after releasing it. We solved this by restarting Jupyter lab every time we needed to use the camera again. In the future the camera will be integrated with everything else.

Some images we got:
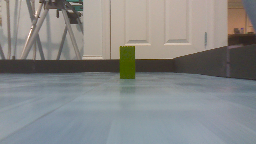
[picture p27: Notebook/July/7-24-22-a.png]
Green obstacle

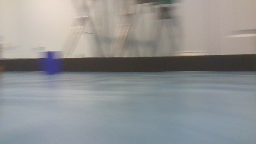
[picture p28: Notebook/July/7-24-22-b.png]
Blurry blue obstacle


Many of them are very blurry because the frame times are so long and we're turning so fast that there ends up being a lot of movement in the time the camera is doing the exposure.

# 7/24/22
The manual drive script now has controller support, making data collection easier. We were able to get images saved from the program. More importantly, we got some AI wall detection working.

Issues we ran into:
* Python script can't save the image, saying "File not found" even though we aren't looking for a file.
* The steering lock broke off again - the metal screws going into nylon caused the threads to strip and the steering locks fell off due to the servo continuously bashing them with the steering arms. The first time we simply used nylon spacers and the original metal screws to solve the issue, but they broke off again. We will be using long nylon screws into nylon spacers from now on.
* Strange errors when trying to send images to control app

We found out that going backwards, the ESC doesn't have as big of a dead zone, and so we can move slower backwards. To take advantage of this feature, we would like to switch the motor to running in the opposite direction, but the ESC doesn't seem to have that feature. However, we think we can "feather" the throttle by quickly alternating between the target throttle and the actual throttle. If done correctly, we can get the slow speed that we currently are unable to use. To be simple, we PWM the PWM to bypass the minimum throttle feature on the ESC.

# 7/25/22
Today we tuned the speed. To "feather" the throttle, we convert the inputted throttle into an active time, a decimal out of 1, where 1 is full power and 0 being no power. That is the active time out of a frequency, so the higher the frequency, the smoother the output is. We can also adjust the drag brake force, which slows the car down in the inactive time. The resulting output alternates between two different PWM states.

# 7/26/22
We began sampling colors for the filter in preparation for training the AI. To do this, we created a simple spreadsheet to hold all the RGB values we sampled, which also had the benefit of being able to automatically calculate the average, median, mode, and range, which we can use to set the target RGB values and tolerances accordingly.

After sampling 12 random images from our first set of training data, we made a filter with some base values and began tuning. The below scene is a good benchmark because it tests a lot of conditions: The traffic signals are facing straight forward or at a diagonal, while being placed really close and also further away, creating lots of contrast and including many cases in one scene.

Original image:

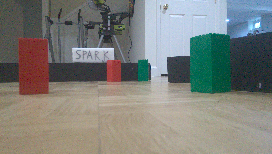
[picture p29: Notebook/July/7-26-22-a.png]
Benchmark image, no filter


First filtered image:

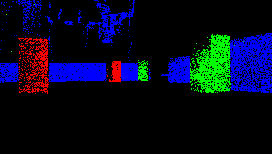
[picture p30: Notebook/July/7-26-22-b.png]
Benchmark image, initial filter


Filtered image after tuning

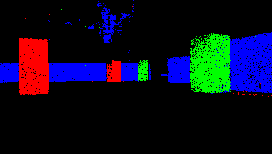
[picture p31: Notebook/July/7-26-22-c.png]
Benchmark image, tuned filter


The outputs are a bit noisy in some spots since the tolerance is a bit too high for comfort. The only real issue is the filtering script is so slow that it's almost unusable for testing, and literally unusable for actual runs. The time taken to apply the filter to one image is 3 seconds - even for the 272x154 images we use. We plan on writing the filter script in C to combat this, though.

# 7/28/22
We won't be using C for the fast filter. It'll be easier to use CV2 to create image masks.

# 7/29/22
The last document was very short. To explain, we're using CV2 to preprocess the images now. Before, we would have a loop going through every pixel of the input image, checking the pixel values against the target. It was uselessly slow, taking 3-4 seconds for one image. We figured out how to speed this up using CV2's built-in `inRange` and `merge` functions. `inRange` will create a mask the same size as the image given to it and will check if the color values are within the bounds inputted. `merge` will take matrices and "merge" them together into another matrix of the same dimensions, but instead of numbers, it contains arrays. The new method can process the same image as much as 30 times faster than using loops.

# 7/30/22
HSV comes with it's own problems. While RGB is harder to use as a filter, red in HSV can range from 0 to 255, meaning since 0 and 255 are both red in that color space. As a result, it is really hard to filter red without adding lots of complexity. Black can also be a hard color to filter, since the hue can be anything, and so there's only value to filter by, since saturation is also all over the place.

We also applied a median blur to the output image to remove noise while preserving edges. The end result is a clean image showing the outlines of everything.

With that working, we began the process of using blob detection for our algorithmic approach. Oh right. We're using two different approaches, in case one doesn't work. The first is more complex, using AI to decide the turning direction. The second is an algorithmic approach.

# 7/31/22
More of the same thing, today we 3D printed some new traffic signals and taped some papers with the correct colors printed onto them onto the traffic signals. We also added a startup script that runs as a startup service. This will make it easier to get the program to run without ssh. Unfortunately the 2 minute boot times are still a big issue that we can't fix.

**WE GOT OUR FIRST AUTONOMOUS TURN!**

Using the height of the pixels in the filtered image, the car can detect walls on the left and right and determine whether to turn left or right in order to avoid the walls!

[Link to video (download)](./July/7-31-22-a.mp4)
[Link to video (download 2)](https://raw.githubusercontent.com/definitely-nobody-is-here/SPARK_Future-Engineers_2022/master/Notebook/2022/July/7-31-22-a.mp4)

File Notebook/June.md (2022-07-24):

# June 2022
SPARK WRO 2022 Future Engineers Engineering Notebooks

***

# 5/30/22
Most of the materials have arrived. Still waiting on ESC and a few bits of hardware.

### Current parts:
* [Schumacher Atom 2 S2 1/12 GT12 Competition Pan Car Kit](https://www.amainhobbies.com/schumacher-atom-2-s2-1-12-gt12-competition-pan-car-kit-schk179/p1055346)
* [Fantom ICON V2 Spec Edition - Sensored Brushless Motor 13.5T](https://fantomracing.com/shop/motors/spec-motors/13-5-icon-v2-works-edition/)
* [Traxxas 48P Pinion Gear w/Set Screw (3.17mm Bore) (19T)](https://urcraceway.com/traxxas-48p-pinion-gear-w-set-screw-3-17mm-bore-19t/)
* [Xceed RC "Enneti" 1/12 Carbon Front Tires (2) (Carbon Black) (40 Shore)](https://www.amainhobbies.com/xceed-rc-enneti-1-12-carbon-front-tires-2-carbon-black-40-shore-xcd101708/p385419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)
* [Xceed RC "Enneti" 1/12 Carbon Rear Tires (2) (Carbon Black) (30 Shore)](https://www.amainhobbies.com/xceed-rc-enneti-1-12-carbon-rear-tires-2-carbon-black-30-shore-xcd101710/p385420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)
* [2x Zeee Premium Series 3S LiPo Battery 4200mAh 11.4V High Voltage Battery 120C with XT60 Plug](https://www.ebay.com/itm/384548969557)
* [2x XL6009 DC-DC 5-32V to 1.25-35V Adjustable Converter Module 4 MOSFET Switch DSN6000AUD](https://www.amazon.com/Automatic-Transformer-Adjustable-Converter-DSN6000AUD/dp/B07LH9H14J)
* [Savox SV1260MG - Mini Digital High Voltage Servo 7.4V](https://www.savoxusa.com/products/savsv1260mg-mini-digital-high-voltage)
* [Woltechz LiPo Battery Charger/Balance/Discharger 1S-6S DC/AC Power Supply for NiMH/NiCD/Li-PO/Li-Fe/Li-ion/PB Packs](https://www.amazon.com/Sky-toy-ST-B6AC-Discharger-Connectors/dp/B07KDSGJFD)
* [ToyBrick TB-RK3399ProD](https://t.rock-chips.com/en/portal.php?mod=view&aid=4) (wrong board)

### Waiting on delivery:
* [HobbyWing QUICRUN 10BL60 Brushless ESC](https://www.hobbywingdirect.com/products/quicrun-wp-10bl60)
* [NVIDIA Jetson NANO](https://developer.nvidia.com/embedded/jetson-NANO-developer-kit)
* Some hardware (M3 spacers, standoffs)

### Progress:
The main chassis has been assembled, except for the ESC. The second layer is not finalized as not all the parts have arrived.

[Spec sheet for Jetson NANO](https://developer.download.nvidia.com/assets/embedded/secure/jetson/NANO/docs/NV_Jetson_NANO_Developer_Kit_User_Guide.pdf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)

***

# 6/4/22

### Updates:
* Jetson NANO has arrived
* Arducam arrived
* The voltage regulators have been replaced with slightly larger ones
* ESC is still in shipping
* Standoffs and spacers have arrived
* The 3D-printed top board is almost ready for printing

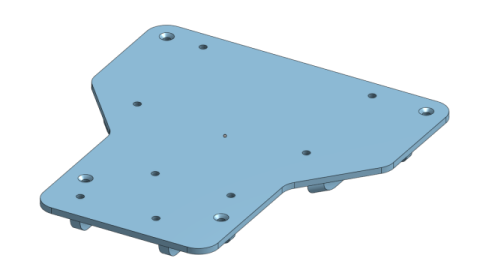
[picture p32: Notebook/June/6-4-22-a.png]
CAD model of 3D printed upper platform


### Current parts:
* [Schumacher Atom 2 S2 1/12 GT12 Competition Pan Car Kit](https://www.amainhobbies.com/schumacher-atom-2-s2-1-12-gt12-competition-pan-car-kit-schk179/p1055346)
* [Fantom ICON V2 Spec Edition - Sensored Brushless Motor 13.5T](https://fantomracing.com/shop/motors/spec-motors/13-5-icon-v2-works-edition/)
* [Traxxas 48P Pinion Gear w/Set Screw (3.17mm Bore) (19T)](https://urcraceway.com/traxxas-48p-pinion-gear-w-set-screw-3-17mm-bore-19t/)
* [Xceed RC "Enneti" 1/12 Carbon Front Tires (2) (Carbon Black) (40 Shore)](https://www.amainhobbies.com/xceed-rc-enneti-1-12-carbon-front-tires-2-carbon-black-40-shore-xcd101708/p385419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)
* [Xceed RC "Enneti" 1/12 Carbon Rear Tires (2) (Carbon Black) (30 Shore)](https://www.amainhobbies.com/xceed-rc-enneti-1-12-carbon-rear-tires-2-carbon-black-30-shore-xcd101710/p385420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)
* [2x Zeee Premium Series 3S LiPo Battery 4200mAh 11.4V High Voltage Battery 120C with XT60 Plug](https://www.ebay.com/itm/384548969557)
* 2x unknown DC to DC voltage regulator
* [Savox SV1260MG - Mini Digital High Voltage Servo 7.4V](https://www.savoxusa.com/products/savsv1260mg-mini-digital-high-voltage)
* [Woltechz LiPo Battery Charger/Balance/Discharger 1S-6S DC/AC Power Supply for NiMH/NiCD/Li-PO/Li-Fe/Li-ion/PB Packs](https://www.amazon.com/Sky-toy-ST-B6AC-Discharger-Connectors/dp/B07KDSGJFD)
* [NVIDIA Jetson NANO](https://developer.nvidia.com/embedded/jetson-NANO-developer-kit)
* [Arducam IMX219 Fixed Focus Camera Module for Nvidia Jetson NANO](https://www.arducam.com/product/b0191-arducam-imx219-visible-light-fixed-focus-camera-module-nvidia-jetson-NANO-raspberry-pi-compute-module/)

***

# 6/5/22

### Updates:
* CAD model for changes made - The Jetson NANO is now rotated 90 degrees to prevent the Arducam's ribbon cable from twisting
* Voltage regulators have been rotated to make soldering easier
* ESC has arrived

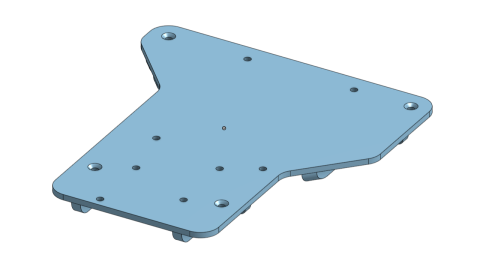
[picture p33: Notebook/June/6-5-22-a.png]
Updated CAD model


### Changes to be made
* [XT 60 battery connectors](https://www.amazon.com/OOOUSE-XT60-Connector-Pairs-pairs/dp/B005FAPYXS) need to be purchased to match connectors on battery
* Special connectors for the servo and ESC have to be made (More to elaborate)

The servo requires a voltage input of 5-7.4V, and the ESC has an output of 6V on the wire to the "receiver". Since we are not using a receiver the 6V power and ground wires on the ESC connector must be removed,leaving a single pin for the PWM input. The servo should not be driven directly from the Jetson NANO since it will only take 5 volts and may draw a lot of current. There are two voltage regulators - one to power the Jetson NANO at 5V and the other can be used to power the servo at 7.4V. Therefore, the connections to the servo and ESC must be modified. The BEC in the ESC must be completely bypassed and the 7.4V input for the servo must be separated to the voltage regulator and the PWM pin for both have to go to the Jetson NANO.

Banana plugs will be soldered to the ESC's ABC connections, to make it removable. A 3-way splitter will be made by soldering 3 16 gauge wire together into one connector.
'
***

# 6/7/22

### Updates:
* Soldered ESC to motor and power
* Tested motor

The motor is too high kV, so it runs way too fast and does not seem to have maximum torque at low RPM. Switching out the motor for a lower kV motor will be better since having a finer range of speed and higher initial torque is better for this application.

Initial tests resulted in the motor starting at full speed and sending the wheels flying off - the clamps for the left wheel weren't tight enough. There's also silicone lubricant everywhere. A higher reduction probably would also help. Since we are using the smallest spur gear we can, we plan to buy a bigger differential gear and put in a smaller spur gear for lower speed and better torque.

***

# 6/11/22

### Updates:
* Changed positions for mounts
* Assembled/soldered parts on upper platform
* Designed mount for camera

The upper platform (platform, Jetson NANO, VRMs) has been soldered and assembled. There is a custom connector for the servo and ESC, with 7.4V running to the servo and their respective PWM pins running to pins 32 and 33 on the Jetson. The platform is mounted in the back where the body posts would be and the front on top of the servo bracket.

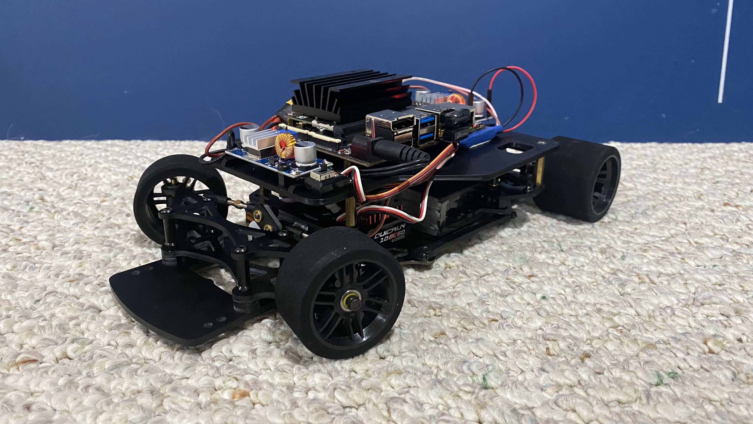
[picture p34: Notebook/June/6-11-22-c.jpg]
Car front left

Car front right
Car rear left

### Changes to parts

Platform V3
#### Changes include:
* Standoff positions moved to allow easier wiring
* Ribs moved on top, now 3mm
* More cutouts on top for better wiring
* Expanded extra surface on top for more space

Camera mount

#### Camera mount
* Features mounting holes for 1 camera configuration and mounting holes for a 2 camera configuration
* Mounts to the front of the car where the bumper would be
* Has holes for LED headlights if needed

***

# 6/17/22

### Updates:
* New 80-tooth diff gear arrived
* Larger wheels being designed
* 40mm fan arrived

The new 90-tooth diff gear arrived, and upon installing, it became apparent that it doesn't fit. Or rather, it barely fits and will get stuck at even the slightest tilt. We'll have to buy a new 84 tooth gear. We have some larger wheels in development to accomodate the new gear. These won't be foam tires and will have a tread, but it shouldn't affect handling.

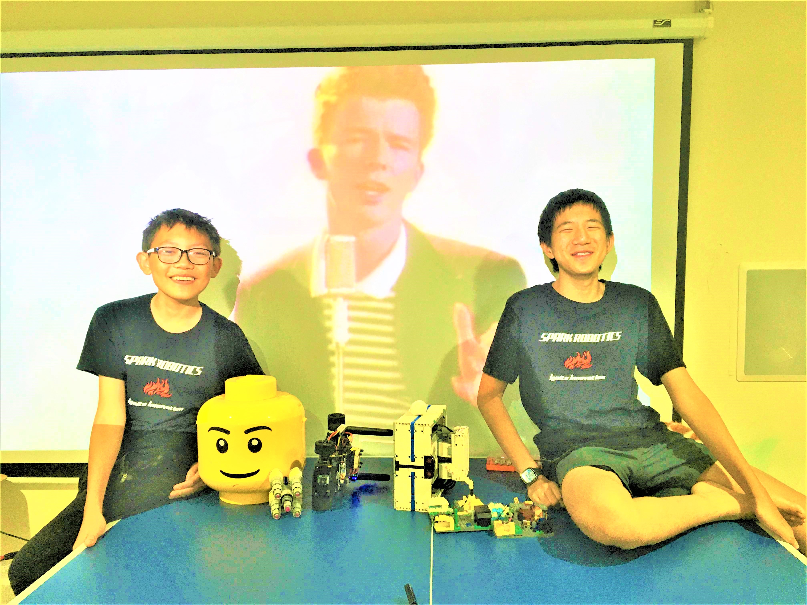
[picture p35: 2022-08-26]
img/bad.JPG

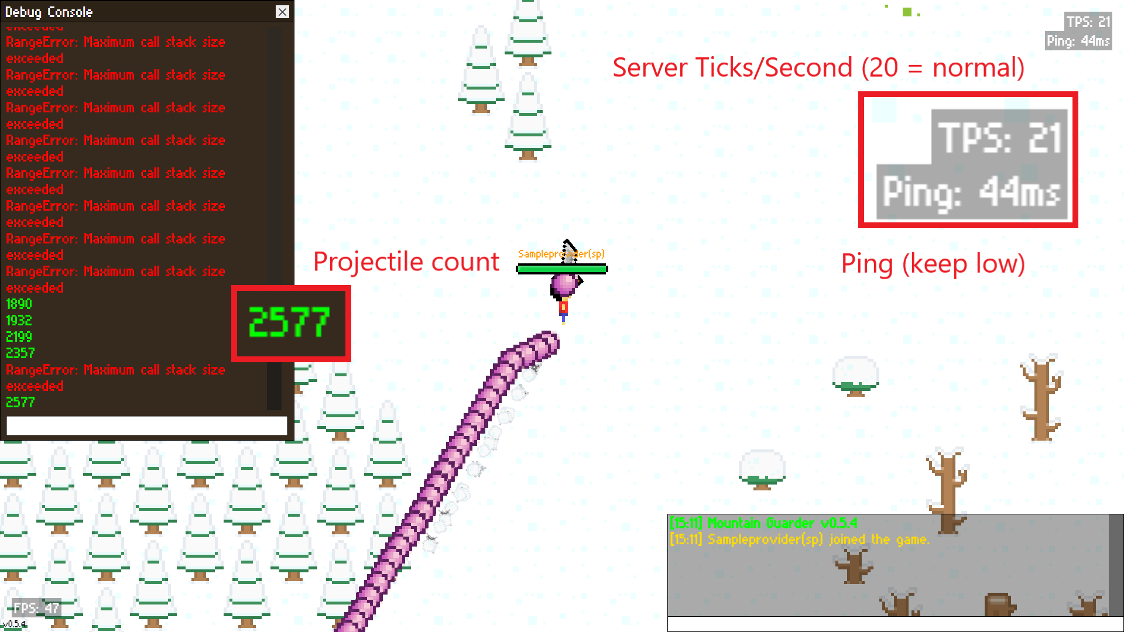
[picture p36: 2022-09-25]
SPARK-Randomiser/images/11-25-21-b.png

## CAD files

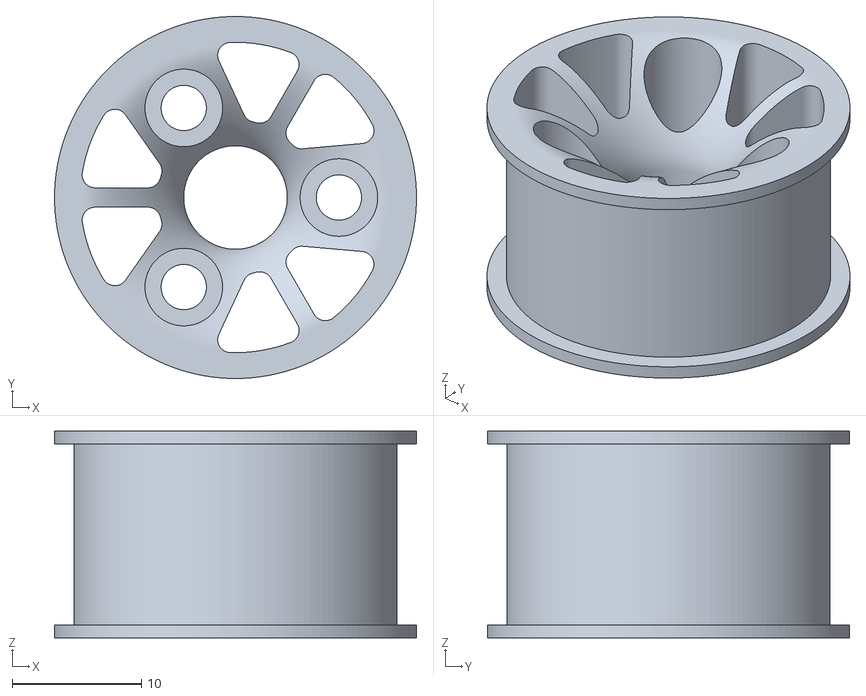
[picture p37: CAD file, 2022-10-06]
Documentation/CAD/history/rear wheel rim v1.stl
28.0 x 28.0 x 16.0

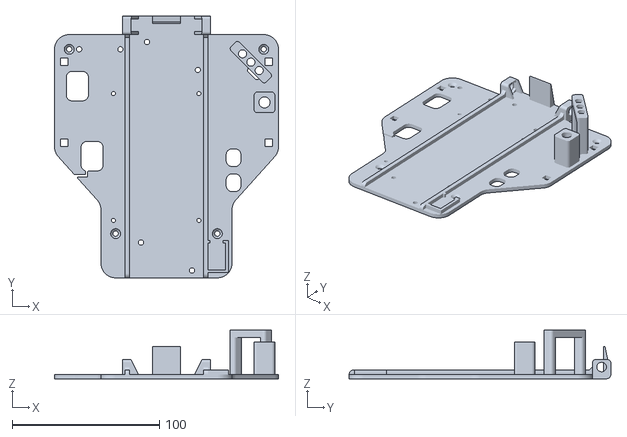
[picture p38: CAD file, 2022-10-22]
Documentation/CAD/SPARK2022_platform.stl
152.0 x 177.6 x 33.0

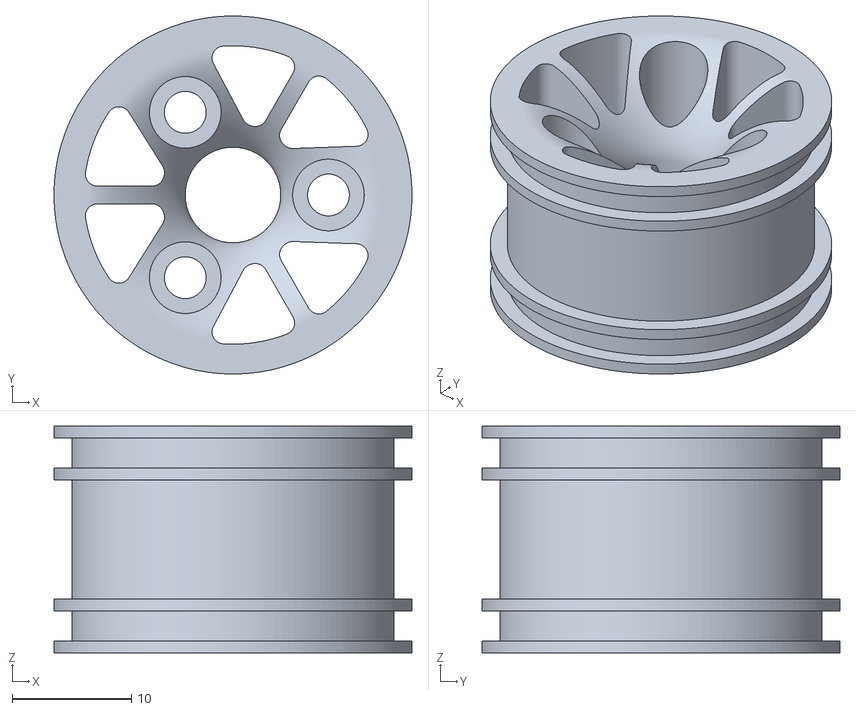
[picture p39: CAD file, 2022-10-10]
Documentation/CAD/SPARK2022_rearwheelrim.stl
30.0 x 30.0 x 19.0

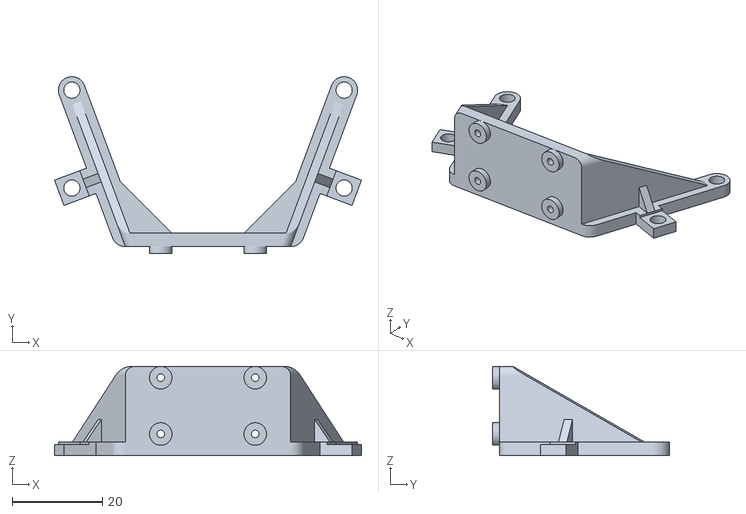
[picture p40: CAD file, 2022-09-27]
Documentation/CAD/history/camera v3.stl
68.2 x 39.2 x 19.8

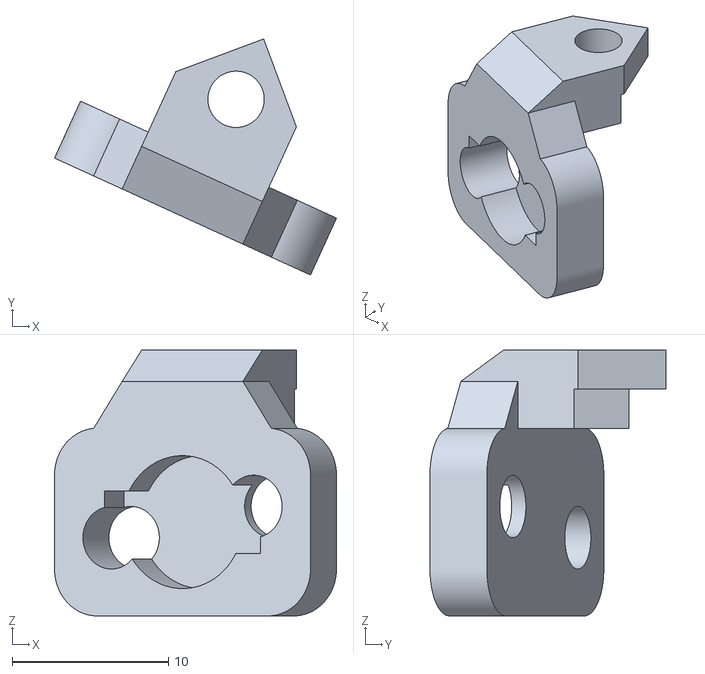
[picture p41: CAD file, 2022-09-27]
Documentation/CAD/SPARK2022_cameraLEDmount.stl
18.0 x 15.1 x 17.0

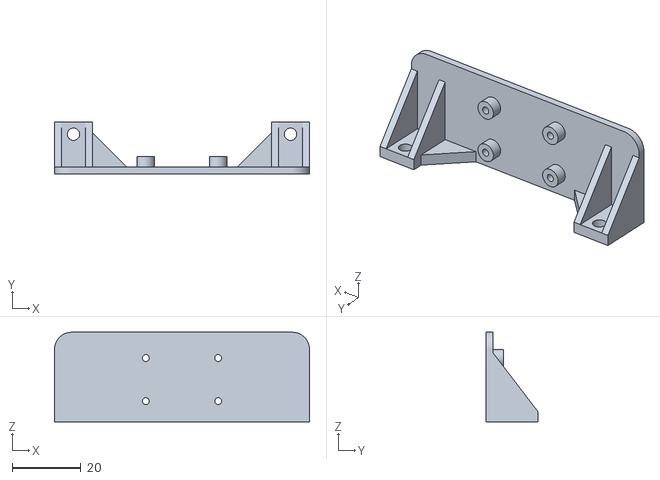
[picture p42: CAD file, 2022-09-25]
Documentation/CAD/SPARK2022_cameramount.stl
74.0 x 15.0 x 26.0

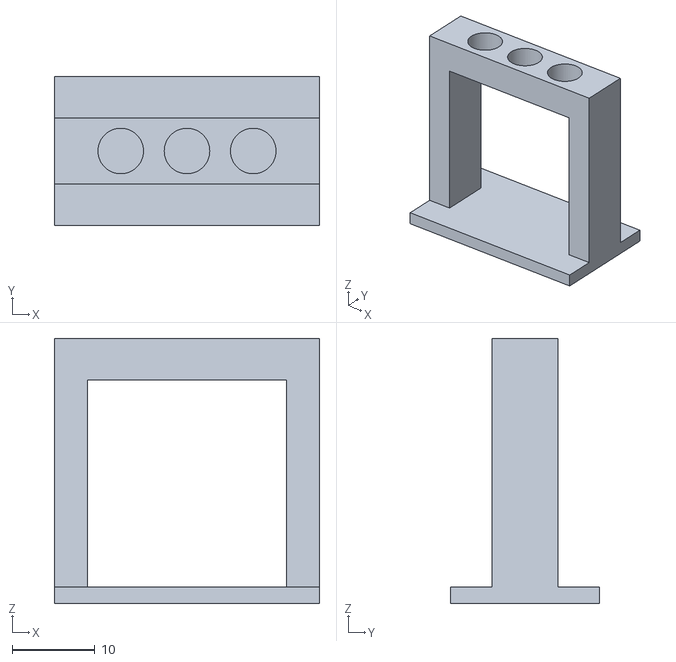
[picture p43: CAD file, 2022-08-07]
Documentation/CAD/history/indicators v1.stl
32.0 x 18.0 x 32.0

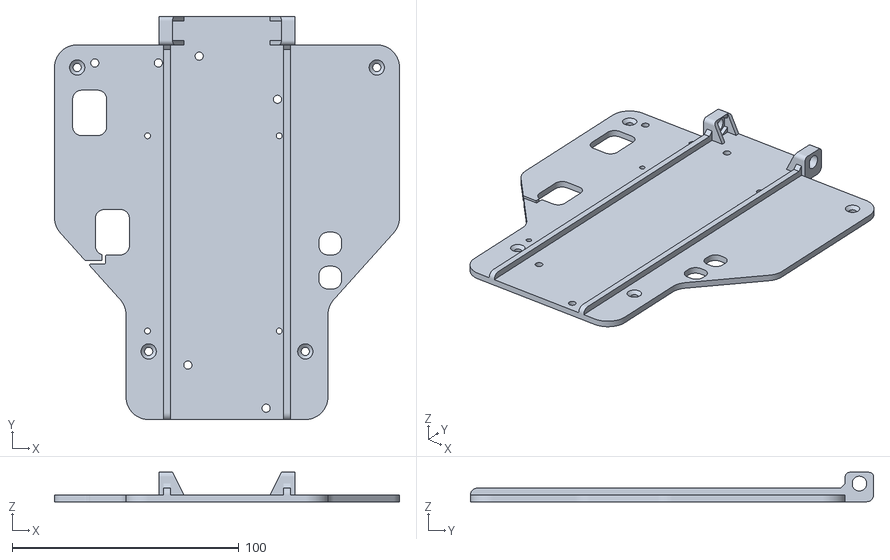
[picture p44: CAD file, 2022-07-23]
Documentation/CAD/history/platform v4.stl
152.0 x 177.6 x 13.0

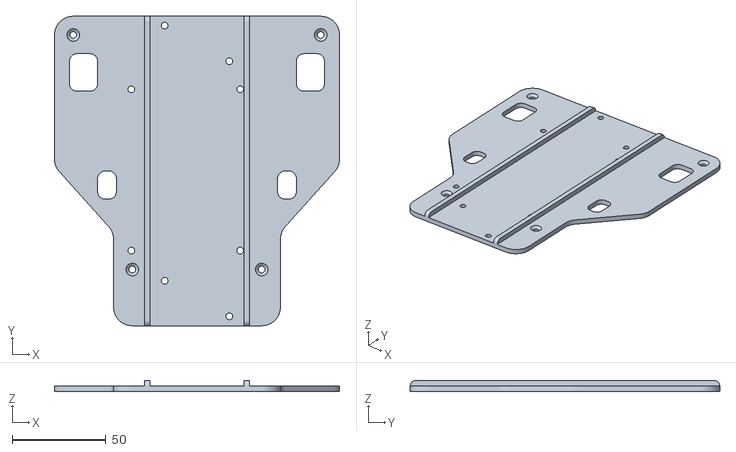
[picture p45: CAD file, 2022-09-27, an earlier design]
Documentation/CAD/history/platform v3.stl
152.0 x 165.1 x 6.00

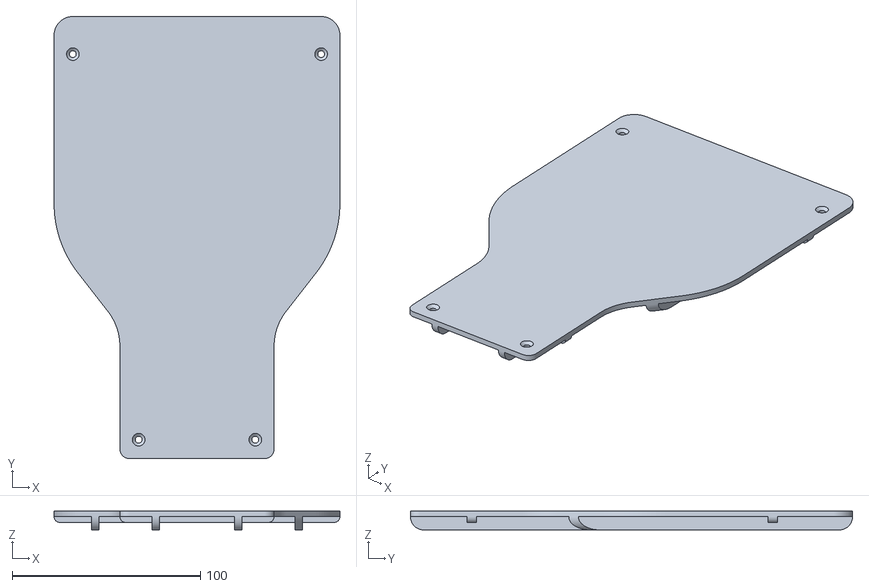
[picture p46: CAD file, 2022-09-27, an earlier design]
Documentation/CAD/history/platform v1.stl
152.0 x 235.0 x 10.0

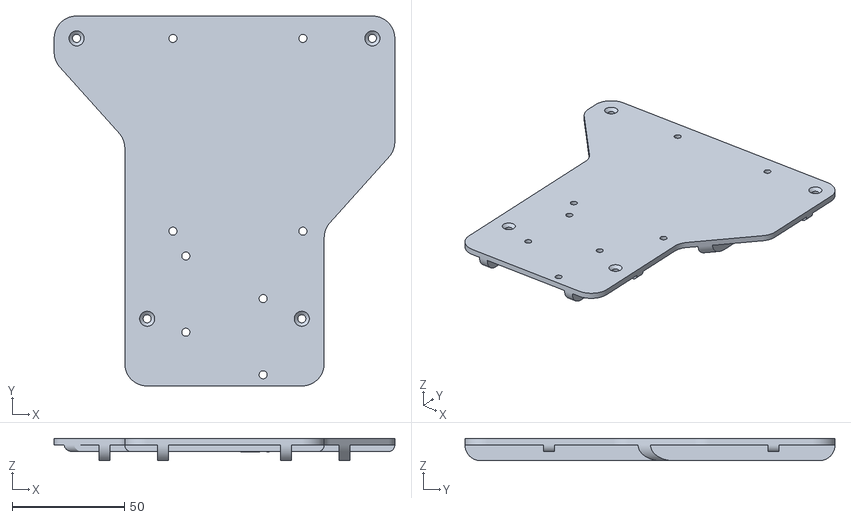
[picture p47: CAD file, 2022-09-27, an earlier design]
Documentation/CAD/history/platform v2.stl
152.0 x 165.1 x 10.0

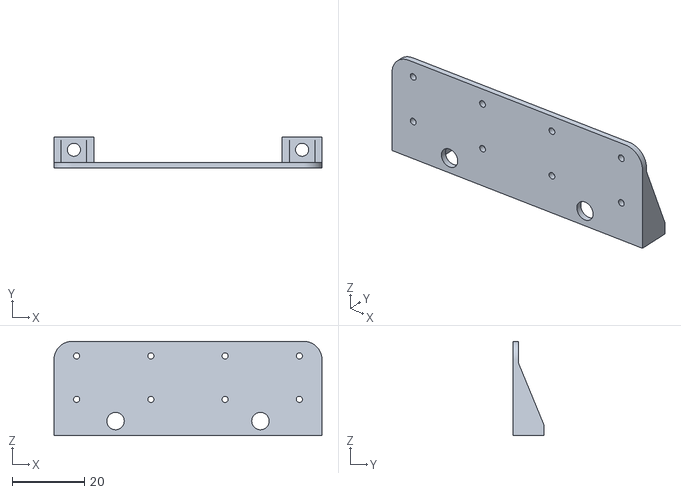
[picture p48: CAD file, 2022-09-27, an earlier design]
Documentation/CAD/history/camera v1.stl
74.0 x 8.50 x 26.0

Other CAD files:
Documentation/CAD/history/camera v2.stl

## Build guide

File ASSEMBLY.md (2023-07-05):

<div align=center>

banner

</div>

***

# **Build Guide**

This is the build guide for our 2022 WRO Future Engineers design - Spark Plugs. It is segmented into 11 main steps, with more detailed steps within. It assumes you have necessary tools and miscellaneous materials including but not limited to: M2.5, M3 driver bits; a Dupont connector crimpange kit; a 3D printer; a soldering iron; 20-24 gauge wire; and M2.5, M3 flat/countersunk screws.

Below is a list of all steps.

***

# Contents

* [Print Parts](#print-parts)
* [Assemble Chassis](#assemble-chassis-kit)
* [ESC, Servo, & Motor](#attach-servo-esc-and-motor)
* [Soldering Electricals](#solder-electrical-components)
    * [Battery Connectors & Voltage Regulator Inputs](#battery-connectors--voltage-regulator-inputs)
    * [Adjusting Voltage Regulators](#adjusting-voltage-regulators)
    * [Voltage Regulator Outputs](#voltage-regulator-outputs)
* [Wiring](#wiring)
* [Jetson NANO Setup](#jetson-nano-setup)
    * [Board Setup, SSHFS, Static IP](#board-setup-sshfs--static-ip)
    * [Enable GPIO & PWM](#enable-gpio-and-pwm)
    * [Remove GUI, Autologin, & Run-on-startup](#text-only-auto-login--run-on-startup)
    * [Fan (optional)](#optional-fan)
* [Standoffs](#platform-standoffs)
* [Platform Assembly](#top-platform-assembly)
* [Camera](#camera-setup)
* [Final Assembly](#plugging-it-all-in)

***

## Print Parts

Before starting assembly, be sure to 3D print all of the 3D-printed parts below:
* [Platform](https://github.com/definitely-nobody-is-here/SPARK_Future-Engineers_2022/raw/master/Documentation/CAD/SPARK2022_platform.stl)
* [Camera Mount](https://github.com/definitely-nobody-is-here/SPARK_Future-Engineers_2022/raw/master/Documentation/CAD/SPARK2022_cameramount.stl)
* [Camera LED Clip](https://github.com/definitely-nobody-is-here/SPARK_Future-Engineers_2022/raw/master/Documentation/CAD/SPARK2022_cameraLEDmount.stl)
* [Rear Wheel Rim](https://github.com/definitely-nobody-is-here/SPARK_Future-Engineers_2022/raw/master/Documentation/CAD/SPARK2022_rearwheelrim.stl)

You can start building while these are printing.

## Assemble Chassis Kit

Our design is built on top of a [Schumacher Atom 2 S2 GT12 Pan Car Kit](https://www.amainhobbies.com/schumacher-atom-2-s2-1-12-gt12-competition-pan-car-kit-schk179/p1055346). Follow the instructions in the box until the step to attach the bumper, which is omitted in our build. Make sure to replace the stock 64-tooth spur gear with a [78-tooth spur gear](https://www.amazon.com/Kimbrough-Pitch-Spur-Gear-78T/dp/B0006O1QVM). Also, remove one layer of spacers from the front suspension to raise the front ride height (the weight of the added componenents cause the front suspension to sag).

At this point, the car should look like the car on the box, except without wheels or a bumper.

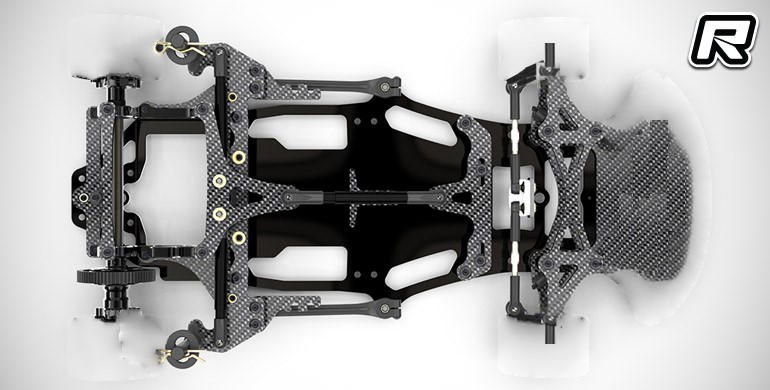
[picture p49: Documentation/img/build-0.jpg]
chassis with modifications


*This image is an edited version of a photo of the carbon fiber edition. It's not ours, we just don't have a picture of this step.*

Take the rear rims and fit the tires onto them. Instructions to attaching wheels are in the kit's instruction packet; follow those to secure the wheels.

## Attach Servo, ESC, & Motor

Use the two included screws in the kit to mount the [Fantom ICON sensored brushless motor](https://fantomracing.com/shop/motors/spec-motors/25-5-icon-torque-works-edition/) to the motor bracket. Then, align the [12-tooth pinion gear](https://www.amazon.com/Traxxas-PINION-PITCH-SCREW-2428/dp/B00EFXMUO2) on the motor shaft and turn the set screw to lock it in place. The servo is placed in the servo bracket (specifics are included in the kit instructions). DO NOT tighten the servo horn to the gear yet, as it must first be centered in order for steering to work. The [HobbyWing Q10BL60 ESC](https://www.hobbywingdirect.com/products/quicrun-10-sensored) can be attached to the forward section using the VHB tape included with it. Make sure to solder the wires in the correct order, or the motor may not rotate. The capacitors for the ESC can be double-sided taped to the forward section as well.

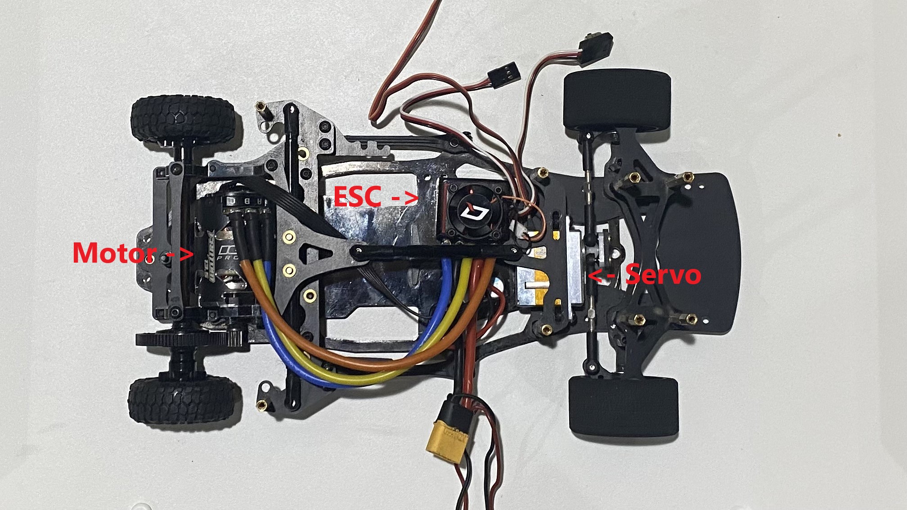
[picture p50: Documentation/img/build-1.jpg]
top-down view


*Our build uses a different 25.5T brushless motor from HobbyWing but we had to modify our chassis to make it fit. The code will still work with the motor in these instructions.*

## Solder Electrical Components

### Battery Connectors & Voltage Regulator Inputs

On the ends of the power leads of the ESC, solder a female XT60 connector and four 20-gauge wires - two on power and two on ground. Make sure it's polarized the same way as the batteries or you risk breaking things. Solder the 20-gauge wires to the inputs of the two [voltage regulators](https://www.amazon.com/Regulator-Adjustable-Converter-Electronic-Stabilizer/dp/B07PDGG84B/ref=sr_1_18). **Ensure that the polarity is correct while soldering.**

### Adjusting Voltage Regulators

Power the regulators by plugging a battery in to the XT60 connector, and change the output voltage of the regulators to 7.4V and 5V. For more information see [this guide by Robottronic](https://www.instructables.com/How-to-Use-DC-to-DC-Buck-Converter-LM2596/).

### Voltage Regulator Outputs

On the output of the 7.4V regulator, solder two single-pin headers. Now, attach the [digital voltometer](https://www.amazon.com/bayite-Digital-Voltmeter-Display-Motorcycle/dp/B00YALUXH0/). On the input, solder the ground wire (black) to the negative terminal, and the power and source wires (red and white) to the positive terminal. On the output of the 5V regulator, solder the [DC barrel jack](https://www.amazon.com/Pigtails-Female-Connector-Pigtail-Security/dp/B08PYWN3T7/) (again, making sure that the polarity is correct). The 7.4V regulator outputs should have two male Dupont connectors soldered to them, facing upwards. This is to make plugging the servos in easier.

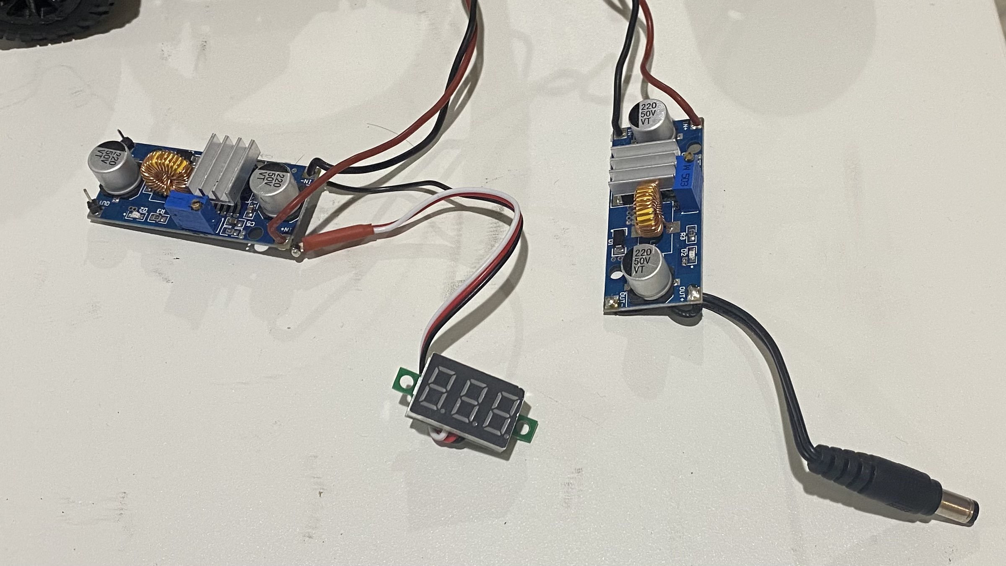
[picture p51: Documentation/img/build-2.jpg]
soldered regulators


## Wiring

*This part of the instructions assumes that you have a dupont connector crimping set*

**Use the diagram in the image below for pin information.**

Crimp 10cm lengths of 20-24 gauge wire to create the servo and ESC connectors. Make sure that the wires are inserted into the connectors in the right order.

Identify the positive and negative terminals of your LEDs if using them. Note that LED indicators are used and will be helpful. Crimp two wires for the negative terminal (-) of the red and green LEDs. Note that the blue power LED has a separate negative wire that leads to a two-pin connector separate from the three-pin connector for the other two, but still goes into the 8-pin connector on the LED end. Again, make sure the wires are in the correct order. Plug the LEDs directly into the 8-pin connector, ensuring correct polarity.

The button must be soldered. The polarity doesn't matter, since it is a simple switch.

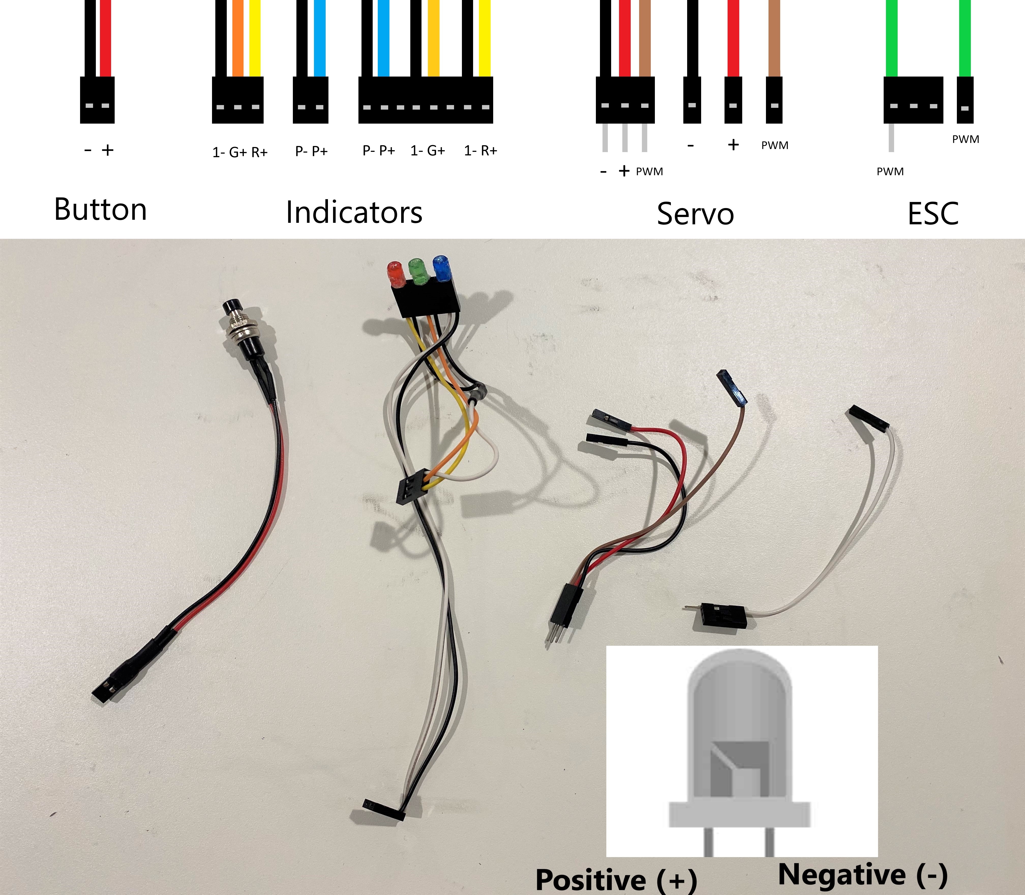
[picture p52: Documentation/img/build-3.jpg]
indicators, connectors, and a button


## Jetson NANO Setup

### Board Setup, SSHFS, & Static IP

Visit [Yahboom](http://www.yahboom.net/)'s [setup and tutorial repository](http://www.yahboom.net/study/jetson-nano) to begin setting up the [Jetson NANO 4GB](https://category.yahboom.net/collections/jetson/products/jetson-nano-sub). Follow steps 1.1-1.7 in "Development setup > SUB Version".

After setting up the board, follow step 2.1 in section "Basic Settings" to log into your Jetson NANO. Keep PuTTY open, as it will be used for the rest of the setup process. Also keep the IP. For remote file transfer, install sshfs (linux only), or use [sshfs-win](https://github.com/winfsp/sshfs-win) from WinFsp. Follow instructions to mount the Jetson NANO to a network drive. Now upload all contents of the `/Program/` folder into a new folder on the Jetson NANO. Remember the directory of the folder, this will be used later.

*This method should be used to upload programs.*

Make sure a static IP is set to the board to make SSH and file transfer easier. Go to your router settings and [assign a DHCP reservation (PCmag)](https://www.pcmag.com/how-to/how-to-set-up-a-static-ip-address) (or a straight static IP) to your Jetson NANO. Save this IP in your PuTTY settings and SSHFS mounting.

Install `websockets` package with pip. <!-- add rest of stuff! -->

### Enable GPIO and PWM

Next, setting up the board for the application. First, enable GPIO and PWM. Create a new user group, and add your user to it (this is the user running the commands).

```
sudo groupadd -f -r gpio
sudo usermod -a -G gpio your_user_name
```

Copy the `99-gpio.rules` file from the `/Program/` folder to `/etc/udev/rules.d/` on the Jetson NANO (use sshfs or ). Then enable the rule.

```
sudo udevadm control --reload-rules && sudo udevadm trigger
```

Now enable PWM. Run the options file for jetson-GPIO.

```
sudo /opt/nvidia/jetson-io/jetson-io.py
```

Go down to "Configure 40-pin expansion header" and enter that submenu. Find `pwm0` and `pwm`, and enable them by selecting them and pressing "Enter". Now exit the tool. GPIO and PWM have been enabled.

### Text-Only, Auto-Login, & Run on Startup

Switch the Jetson NANO to text-only mode (gui is almost useless for this application and only causes unneccesary slowness).

```
sudo systemctl set-default multi-user.target
```

Autologin must be done to avoid having to plug in a monitor and keyboard to start ssh and run programs. The following accomplishes it:

```
sudo systemctl edit getty@tty1
```

A temporary editor will appear. Place the following text in it, replacing "your_user_name" with your user name.

```
[Service]
ExecStart=
ExecStart=-/sbin/agetty -o '-p -f your_user_name' -a your_user_name --noclear %I $TERM
```

Save and close the editor with `:wqa`.

To run the program on startup, first obtain the directory of the program folder uploaded earlier. Create `spark_startup.service` in `/etc/systemd/system` and place the following in the contents, replacing "/filepath/" with the absolute directory of the folder (begins with a "/").

<!-- specify filepath? -->
<!-- switch to bashrc? -->
```
[Service]
ExecStart=cd /filepath /usr/bin/python3 /filepath/startup.py
User=username

[Install]
WantedBy=multi-user.target
```

Save the file and add permissions to it.

```
sudo chmod 644 /etc/systemd/system/spark_startup.service
systemctl enable spark_startup.service
```

Reboot the Jetson NANO to test if these changes worked. No GUI should appear and you shuld be automatically logged in.

Enable run-on-startup by editing `run-on-startup.txt` in the folder. Replace the first line with `true`.

Go through `startup.py` and `/IO/io.py`, and change `path` to the absolute filepath of your directory (same as filepath in the previous steps)

Example:

```
path = '/home/nano/Documents/SPARK_FutureEngineers_2022/'
```

Reboot the Jetson NANO again

### Optional Fan

Add the [Noctua NF-A4X10 5V PWM fan](https://noctua.at/en/products/fan/nf-a4x10-5v) to the board using M3x20mm nylon screws. Metal screws may be required to "tap" the holes (it's best to use an actuall tapper, though).

## Platform Standoffs

Follow the diagram below to place the spacers and standoffs for the mounting of the upper platform and camera. The rear two are spacers, and the other six will replace existing screws.

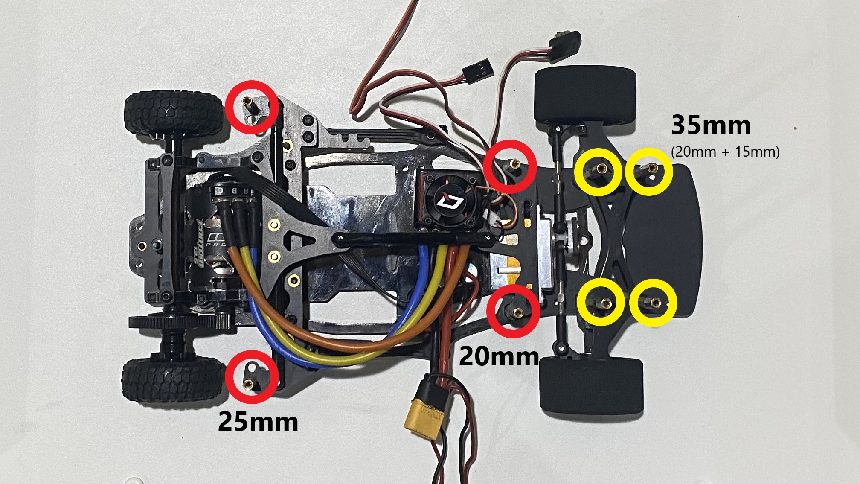
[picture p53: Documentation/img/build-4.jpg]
standoff/spacer locations


Use the diagram below to fill in the standoffs on the top platform. All standoffs in green are M3x6mm nylon standoffs, and the blue are M2.5x5mm brass spacers (included with Jetson NANO). Use M3 nylon nuts to hold the nylon standoffs onto the board and use 8mm M2.5 screws to hold the brass spacers onto the board.

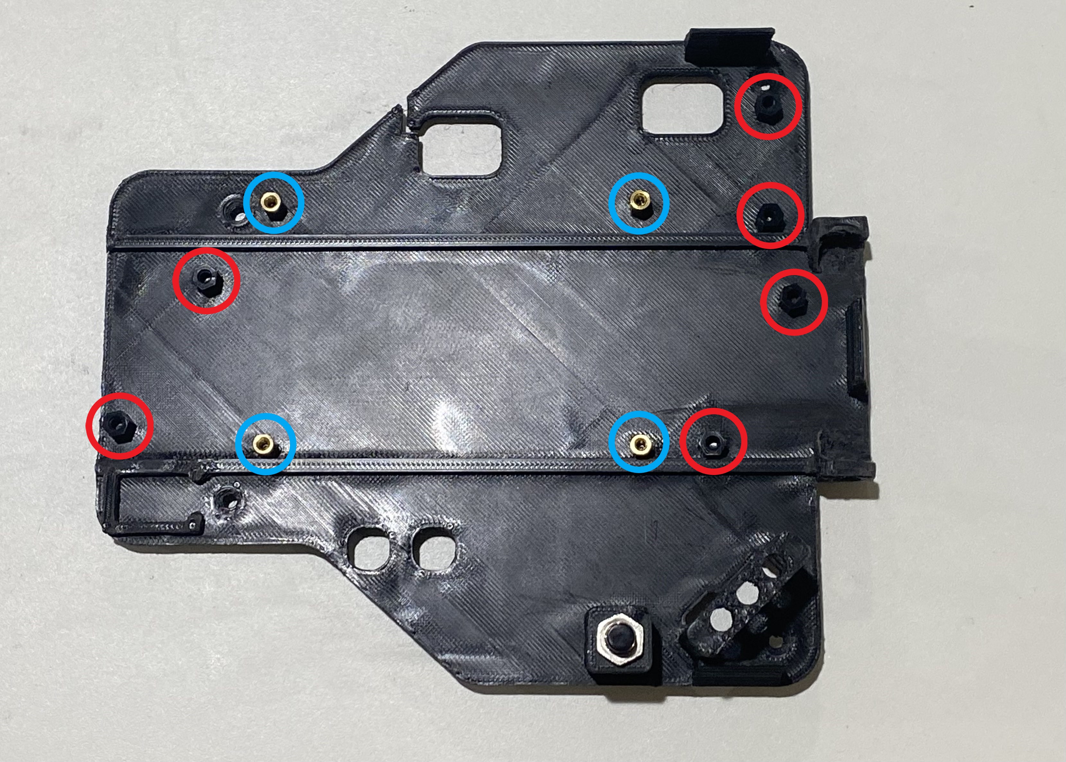
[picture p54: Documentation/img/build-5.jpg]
standoff locations on platform


*Note: Platform in diagram is of a slightly older design of V5. Standoff and spacer locations still apply.*

## Top Platform Assembly

Place the top platform assembly on top of the 25mm/20mm brass standoffs mentioned [earlier](#platform-standoffs). Screw them in using M3x6mm countersunk screws. Route the wires through the provided cable management holes. The way they are routed doesn't matter, but the use the image below for a general guide on routing wires. The [voltage regulators](#voltage-regulators) are attached to the [diagonal nylon spacers (image 2, red)](#platform-standoffs) with 6mm M3 nylon screws, with the outputs facing toward the side with the [button and indicator LEDS](#wiring), as well as the 5V regulator being in the front (narrow end) and the 7.4V regulator in the back (LED indicator end). The voltometer](https://www.amazon.com/bayite-Digital-Voltmeter-Display-Motorcycle/dp/B00YALUXH0/) goes on the [two nylon standoffs (image 2, red)](#platform-standoffs) on the input side of the 7.4V regulator.

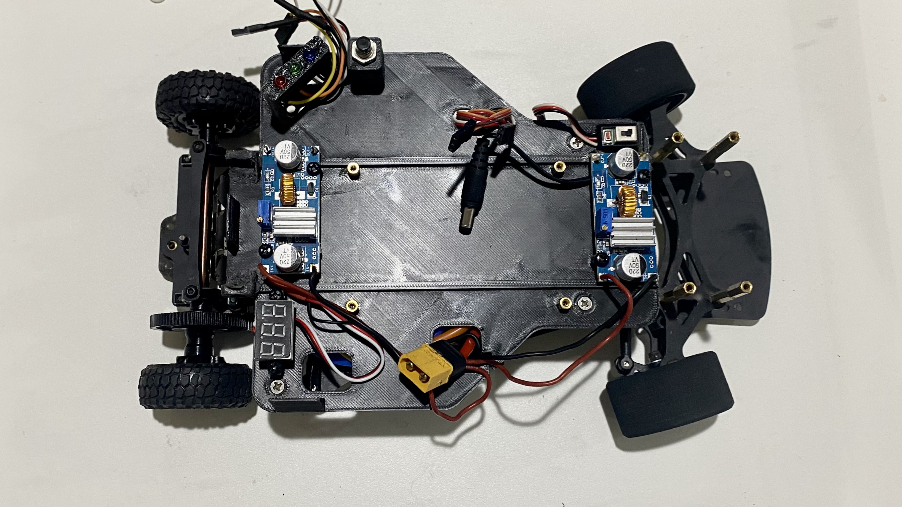
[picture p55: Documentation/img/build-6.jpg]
platform mounted with voltage regulators


Place the [assembled Jetson NANO](#jetson-nano) on the [four brass standoffs (image 2, blue)](#platform-standoffs) and secure with the provided M2.5x5mm screws. If there is a [WiFi card](https://www.newegg.com/p/0XM-009Y-001C7), route the antenna cables to the rear (right of image) and attach to the holders.

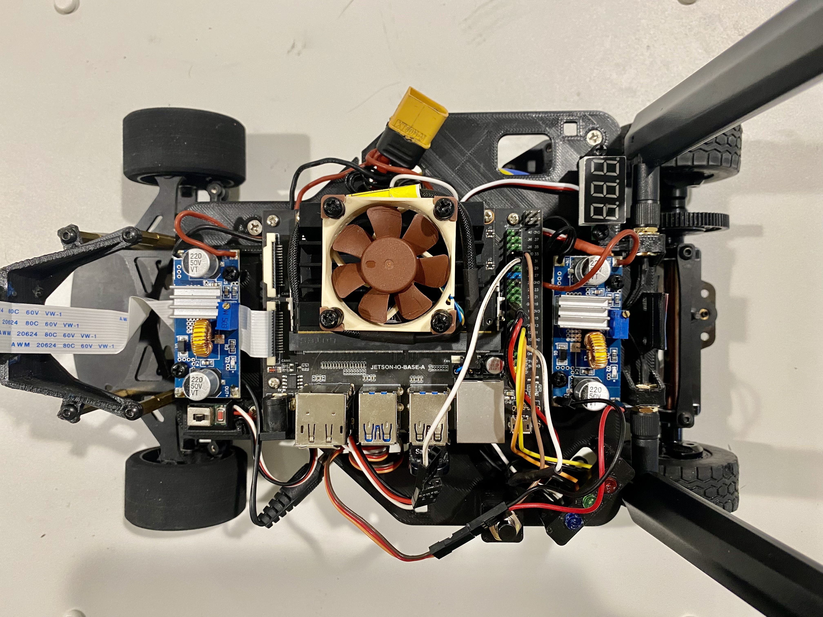
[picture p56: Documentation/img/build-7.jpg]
platform with everything mounted


## Camera Setup
Follow instructions to assemble the [Arducam IMX219 175 Degree camera](https://www.amazon.com/Arducam-Raspberry-Official-Megapixel-Replacement/dp/B083PW4BLH/). Use M2.5x4mm screws to mount the camera onto the front of camera bracket. Make sure the CSI slot is on the top side.

Screw the camera bracket onto the [four brass standoffs (image 1, yellow)](#platform-standoffs) in the front of the car.

Later, focus the camera and make it slightly blurry - this filters some far-away noise in the image without impacting performance.

## Plugging it All In

check wiring

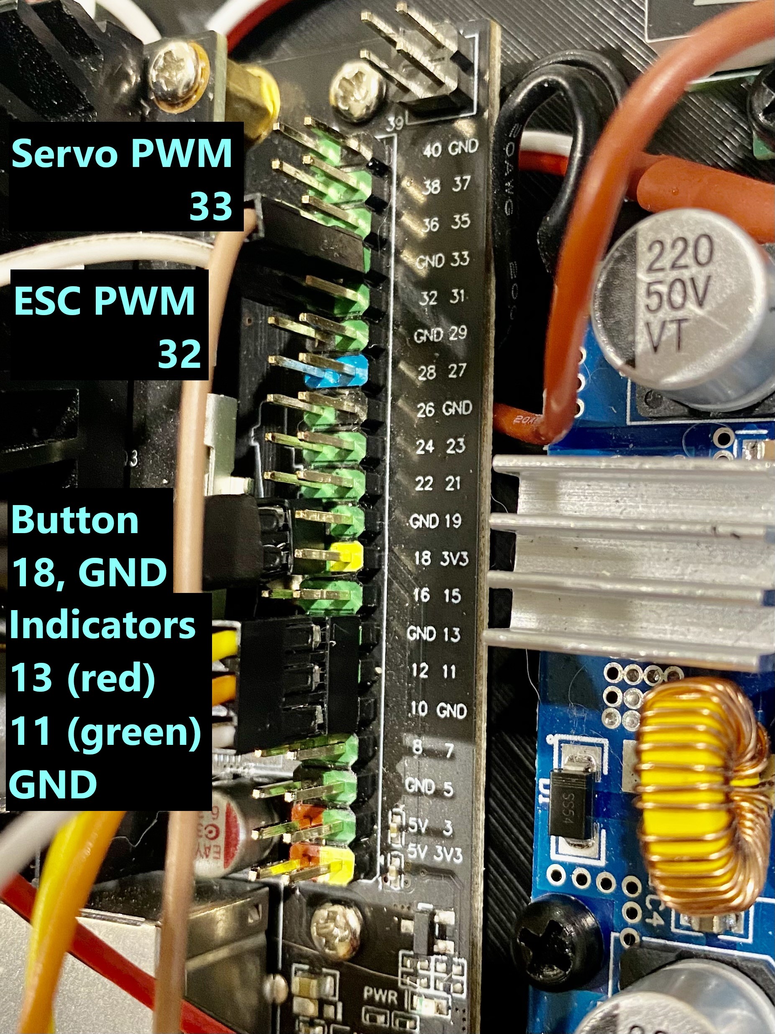
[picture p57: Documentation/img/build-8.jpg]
pin numberings


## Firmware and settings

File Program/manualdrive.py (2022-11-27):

from IO import io
io.setup()
from IO import drive
from IO import camera
from Util import server
from AI import filter
from threading import Thread
import cv2
import time
import base64

__forward = 0
__backward = 0
__left = 0
__right = 0
running = True
streamThread = None
streamThread2 = None
streaming = False
streaming2 = False
def main():
    global running
    try:
        io.setStatusBlink(2)
        server.open()
        drive.start()
        camera.start()
        def keys(data):
            global __forward, __backward, __left, __right
            key = data['key']
            if key == 'w':
                __forward = 100
            elif key == 'W':
                __forward = 0
            elif key == 's':
                __backward = -100
            elif key == 'S':
                __backward = 0
            elif key == 'a':
                __left = -100
            elif key == 'A':
                __left = 0
            elif key == 'd':
                __right = 100
            elif key == 'D':
                __right = 0
            drive.throttle(__forward+__backward)
            drive.steer(__left+__right)
        def joystick(data):
            __forward = max(data['throttle'], 0)
            __backward = min(data['throttle'], 0)
            __left = min(data['steering'], 0)
            __right = max(data['steering'], 0)
            drive.throttle(__forward+__backward)
            drive.steer(__left+__right)
        def capture(data):
            camera.capture(server=server, drive=drive)
        def captureStream(data):
            if data['state'] == True:
                camera.startSaveStream(server=server, drive=drive)
            else:
                camera.stopSaveStream(server)
        def captureFilter(data):
            filter.setColors(data, server=server)
            camera.capture(filter=filter, server=server, drive=drive)
        def captureFilterStream(data):
            filter.setColors(data['colors'])
            if data['state'] == True:
                camera.startSaveStream(filter=filter, server=server, drive=drive)
            else:
                camera.stopSaveStream(server)
        def stream(data):
            global streamThread, streaming
            if data['state'] == True:
                if streaming == False:
                    streaming = True
                    def loop():
                        global streaming, running
                        try:
                            while streaming and running:
                                start = time.time()
                                encoded = base64.b64encode(cv2.imencode('.png', camera.read())[1]).decode()
                                server.broadcast('capture', encoded)
                                time.sleep(max(0.1-(time.time()-start), 0))
                        except Exception as err:
                            print(err)
                    streamThread = Thread(target = loop)
                    streamThread.start()
                    server.broadcast('message', 'Began stream')
            else:
                if streaming == True:
                    streaming = False
                    streamThread.join()
                    server.broadcast('message', 'Ended stream')
        def filterstream(data):
            global streamThread2, streaming2
            filter.setColors(data['colors'])
            if data['state'] == True:
                if streaming2 == False:
                    streaming2 = True
                    def loop():
                        global streaming2, running
                        try:
                            while streaming2 and running:
                                start = time.time()
                                encoded = base64.b64encode(cv2.imencode('.png', filter.filter(camera.read(), False))[1]).decode()
                                server.broadcast('capture', encoded)
                                time.sleep(max(0.05-(time.time()-start), 0))
                        except Exception as err:
                            print(err)
                    streamThread2 = Thread(target = loop)
                    streamThread2.start()
                    server.broadcast('message', 'Began filtered stream')
            else:
                if streaming2 == True:
                    streaming2 = False
                    streamThread2.join()
                    server.broadcast('message', 'Ended filtered stream')
        def view(data):
            encoded = base64.b64encode(cv2.imencode('.png', camera.read())[1]).decode()
            server.broadcast('capture', encoded)
        def viewFilter(data):
            filter.setColors(data)
            encoded = base64.b64encode(cv2.imencode('.png', filter.filter(camera.read(), False))[1]).decode()
            server.broadcast('capture', encoded)
        def prediction(data):
            filter.predict(camera.read(), server, False)
            server.broadcast('message', 'Ran prediction on image')
        def colors(data):
            filter.setColors(data)
        server.addListener('key', keys)
        server.addListener('joystick', joystick)
        server.addListener('capture', capture)
        server.addListener('captureStream', captureStream)
        server.addListener('colors', colors)
        server.addListener('captureFilter', captureFilter)
        server.addListener('captureFilterStream', captureFilterStream)
        server.addListener('view', view)
        server.addListener('viewFilter', viewFilter)
        server.addListener('stream', stream)
        server.addListener('filterstream', filterstream)
        server.addListener('prediction', prediction)
        global running
        running = True
        def stop(data):
            global running
            running = False
            io.setStatusBlink(0)
            camera.stop()
            server.close()
            drive.stop()
            io.close()
            print('stopped by emergency stop button')
            exit(0)
        server.addListener('stop', stop)
        while running:
            msg = input()
            if msg == 'reset':
                server.broadcast('colors', filter.setDefaultColors())
            elif msg != '':
                server.broadcast('message', msg)
    except KeyboardInterrupt:
        print('\nSTOPPING PROGRAM. DO NOT INTERRUPT.')
        running = False
        camera.stop()
        server.close()
        drive.stop()
        io.close()
    except Exception as err:
        print(err)
        io.error()

if __name__ == '__main__':
    main()

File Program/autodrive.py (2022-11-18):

from IO import io
io.setup()
from IO import drive
from IO import camera
from Util import server
from AI import filter
import time
import sys

running = True
def main():
    global running
    try:
        io.setStatusBlink(0)
        infinite = False
        wait = False
        openServer = True
        for i, arg in enumerate(sys.argv):
            if i != 0:
                if arg == 'infinite':
                    infinite = True
                if arg == 'wait_for_button':
                    wait = True
                if arg == 'no_server':
                    openServer = False
        if infinite:
            print('PROGRAM RUNNING IN INFINITE MODE!')
        if openServer:
            server.open()
        drive.start()
        camera.start()
        io.setStatusBlink(1)
        if wait:
            print('Waiting for button')
            io.waitForButton()
        else:
            time.sleep(1)
        io.setStatusBlink(2)
        def stop(data):
            global running
            running = False
            io.setStatusBlink(0)
            camera.stop()
            server.close()
            drive.stop()
            io.close()
            print('stopped by emergency stop button')
            exit(0)
        def stop2(data):
            global running
            running = False
            io.setStatusBlink(0)
            camera.stop()
            server.close()
            drive.stop()
            io.close()
            print('stopped by 3 laps')
            exit(0)
        server.addListener('stop', stop)
        drive.throttle(50)
        while running:
            image = camera.read()
            prediction = filter.predict(image,server, infinite)
            if prediction == "stop":
                # drive.throttle(-20)
                drive.steer(0)
                # time.sleep(0.2)
                drive.throttle(0)
                time.sleep(0.2)
                stop2(1)
                break
            drive.steer(prediction)
            # print("Current Prediction: " + str(prediction))
        #code here
    except KeyboardInterrupt:
        camera.stop()
        drive.stop()
        io.close()
    except Exception as err:
        print(err)
        io.error()

if __name__ == '__main__':
    main()

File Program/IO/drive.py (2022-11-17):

import Jetson.GPIO as GPIO
from threading import Thread
from IO import io
import time

# drive module for controlling throttle and steering output

# setup
t = GPIO.PWM(32, 500)
s = GPIO.PWM(33, 200)

# pwm min max and speed
thrBACK = 70
thrMIN = 75
thrMAX = 80
thrBACK2 = 1_400_000
thrMIN2 = 1_500_000
thrMAX2 = 1_550_000
strMAX = 47
strMIN = 28
strTRIM = 8
# throttle feathering
# thrFeaFREQ = 10
# thrFeaDiv = 20
# control variables
targetThrottle = 0
targetSteering = 0
currThrottle = 0
currSteering = 0
steerSpeed = 0.3
# control loop
tickrate = 200
running = False
controlThread = None

def start():
    global controlThread, running
    if running == False:
        # begin
        running = True
        t.start(thrMIN)
        s.start((strMIN+strMAX)/2)
        def loop():
            try:
                # global running, t, s, currThrottle, currSteering, targetThrottle, targetSteering, thrFeaFREQ, thrFeaDiv, tickrate
                global running, t, s, currThrottle, currSteering, targetThrottle, targetSteering, steerSpeed, tickrate
                # timer = 0
                while running:
                    start = time.time()
                    # convert throttle to active time
                    # thrFeaACT = math.floor(abs(targetThrottle)/20)/thrFeaDiv
                    # if timer >= 1: timer = 0
                    # if timer <= thrFeaACT and thrFeaACT < 1 and targetThrottle > 10: currThrottle = 100
                    # elif targetThrottle < -10 or thrFeaACT >= 1: currThrottle = targetThrottle
                    # else: currThrottle = 0
                    currThrottle = targetThrottle
                    currSteering = targetSteering*steerSpeed + currSteering*(1-steerSpeed)
                    # apply throttle and steering
                    if (currThrottle < 0): t.ChangeDutyCycle((currThrottle/100)*(thrMIN-thrBACK)+thrMIN)
                    else: t.ChangeDutyCycle((currThrottle/100)*(thrMAX-thrMIN)+thrMIN)
                    # if (currThrottle < 0): GPIO._set_pwm_duty_cycle(t._ch_info, (currThrottle/100)*(thrMIN2-thrBACK2)+thrMIN2)
                    # else: GPIO._set_pwm_duty_cycle(t._ch_info, (currThrottle/100)*(thrMAX-thrMIN)+thrMIN)
                    s.ChangeDutyCycle((currSteering/100.0)*((strMAX-strMIN)/2)+((strMIN+strMAX)/2)+(strTRIM/10))
                    # advance timer
                    # timer += thrFeaFREQ/tickrate
                    time.sleep(max((1/tickrate)-(time.time()-start), 0))
            except Exception as err:
                print(err)
                io.error()
        controlThread = Thread(target = loop)
        controlThread.start()
        return True
    return False

def stop():
    global running, controlThread
    if running == True:
        running = False
        controlThread.join()
        t.ChangeDutyCycle(thrMIN)
        s.ChangeDutyCycle((strMIN+strMAX)/2)
        t.stop()
        s.stop()
        return True
    return False

# inputs
def steer(steering: int):
    global targetSteering
    targetSteering = max(-100, min(-steering, 100))

def throttle(throttle: int):
    global targetThrottle
    targetThrottle = max(-100, min(throttle, 100))

def trim(trim: int):
    global strTRIM
    strTRIM = trim

# get current
def currentSteering():
    global currSteering
    return -currSteering

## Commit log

2022-07-22 very broken server code
    how is it so broken
    [drive-test.py, drive.py]
2022-07-22 Fix server
    somehow there are errors now
    [drive-test.py]
2022-07-22 changes to PWM values
2022-07-23 do stuff
    [SPARK2022_cameramount.stl, SPARK2022_platform.stl]
2022-07-23 the E
    EEEE
    camera
2022-07-23 camera stuff
2022-07-23 fix stuff
    also camera capture works
    [camera.py, drive-test.py]
2022-07-24 a painful attempt to fixing the camera
    [camera.py, io.py, manualdrive.py]
2022-07-24 somehow fixed the camera
    [camera.py, manualdrive.py]
2022-07-24 fixed save images
    still no send to client
    [camera.py]
2022-07-24 fix camera code and stuff
    [camera.py, manualdrive.py]
2022-07-24 fix camera save stream and joystick touch support
    [camera.py, manualdrive.py]
2022-07-25 add throttle feathering
2022-07-25 fixthrottle feathering
    and also fix other things
    i should fix the commit name
    [camera.py, drive.py, manualdrive.py]
2022-07-26 add filter (still in testing)
2022-07-26 fix camera fov
    we still need a wider angle camera
    [camera.py]
2022-07-26 improve filter
2022-07-29 image filter works
2022-07-30 why is filter broken
2022-07-30 tune filter
2022-07-31 add steering value logs
2022-07-31 fix steering logging
2022-07-31 add python script on startup
    this took way too long
    [startup.py]
2022-08-01 its 11:30 but i had an idea so i made some changes
    hopefully no crash?
    [camera.py, manualdrive.py]
2022-08-04 tune filter and add IMAGE DISPLAY
2022-08-06 tune filter for new red
2022-08-09 fix camera server still borok
    [camera.py]
2022-08-09 filter again
2022-08-09 tune filter
    its still too loose and sometimes there are conflicts
2022-08-15 change filter
2022-08-24 rulebook added just in case
2022-08-27 bugfixes to filter
2022-08-27 fix filter
2022-08-27 Jetson Banano
2022-08-27 Revert "Jetson Banano"
    This reverts commit f89d7ff46aadc8452dce3d1b5ccd92d59d413985.
2022-08-27 omg jetson banano confirmed
2022-08-27 jetson banano v2
2022-09-01 dsfhgjfkyu gv
    [SPARK2022_cameramount.stl, camera mount.stl]
2022-09-26 cad things
    [SPARK2022_LEDmount.stl, SPARK2022_cameraLEDmount.stl, camera v3.stl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]
2022-10-03 DOCUMENTATION
    DOCUMENTATIONDOCUMENTATIONDOCUMENTATIONDOCUMENTATIONDOCUMENTATIONDOCUMENTATIONDOCUMENTATIONDOCUMENTATIONDOCUMENTATIONDOCUMENTATIONDOCUMENTATIONDOCUMENTATIONDOCUMENTATIONDOCUMENTATIONDOCUMENTATIONDOCU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
    [SPARK2022_rearwheelrim.stl]
2022-10-06 a wheely bad pun
    [SPARK2022_rearwheelrim.stl, rear wheel rim v1.stl]
2022-10-22 docs
    and other things
    [SPARK2022_platform.stl]
2022-10-29 Summary (required)
    Description
    [clanBoosts.csv, crafts.csv, items.csv]
2022-10-29 Revert "Summary (required)"
    This reverts commit 775bf986e53e49c446fb6cc9167d7f701e11f6fc.
    [clanBoosts.csv, crafts.csv, items.csv]
2022-12-15 I heard you like camera shake
